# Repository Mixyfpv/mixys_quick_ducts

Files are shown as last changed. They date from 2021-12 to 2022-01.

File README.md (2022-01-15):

# Mixy's Quick Ducts
## What this is
Mixy's Quick Ducts are 5 inches ducts designed to fit most - if not all - 5 inch FPV drones in production today.

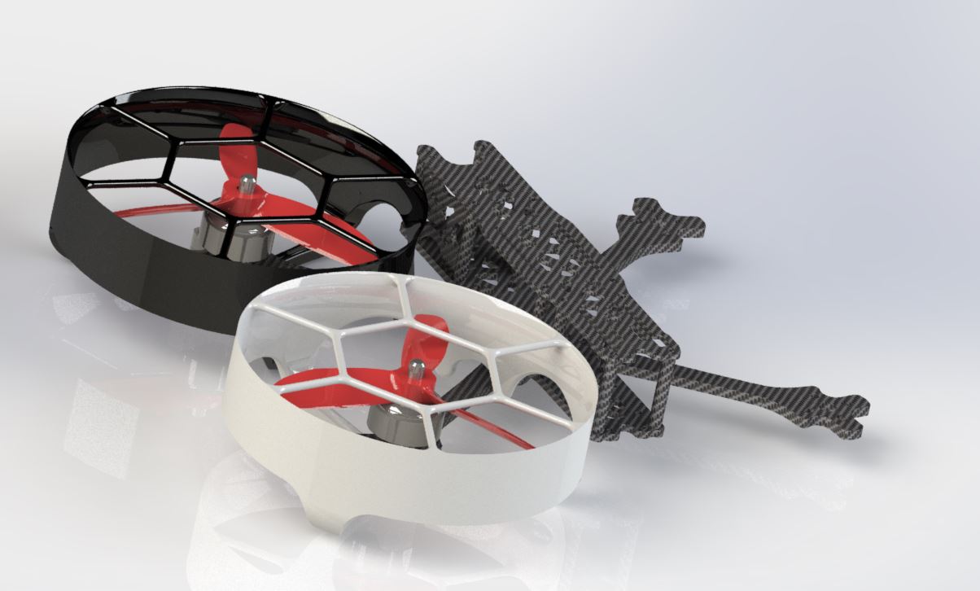
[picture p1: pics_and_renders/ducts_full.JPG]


These ducts were designed with one goal in mind, to be easy to use, and to be faster to put on and off your drone than currently available commercial solutions, as well as providing protection for bystanders when flying.

The ducts sit around the propeller disc. Their inside diameter is 5 inches.

It is expected that the duct will grind a bit of the props and its inside once you started the motors for the simple reason that the prop manufacturers tolerance to prop diameter varies. A lot. Around +- 1 mm. That is why you should not expect the prop to be perfectly flush against the inside of the duct.
3D printing imperfectiosn might also impact this.

The curve of the duct wall is an Eppler 423 airfoil which appear to be very suited for this use :
http://airfoiltools.com/airfoil/details?airfoil=e423-il

This ducts can be 3D printed. It has been tested with PLA+, regular PLA and PETG.
The arm mounts must be printed out of TPU.

## Some pics and renders

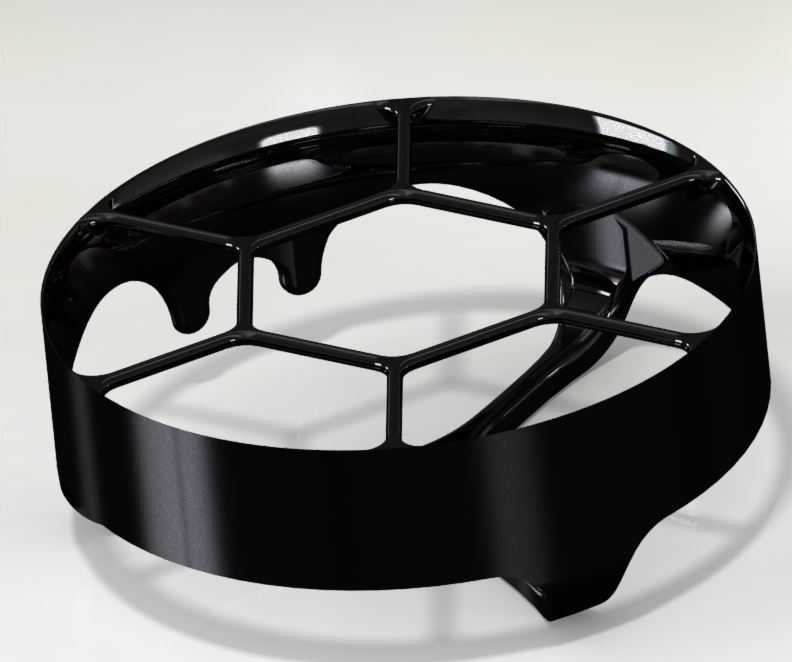
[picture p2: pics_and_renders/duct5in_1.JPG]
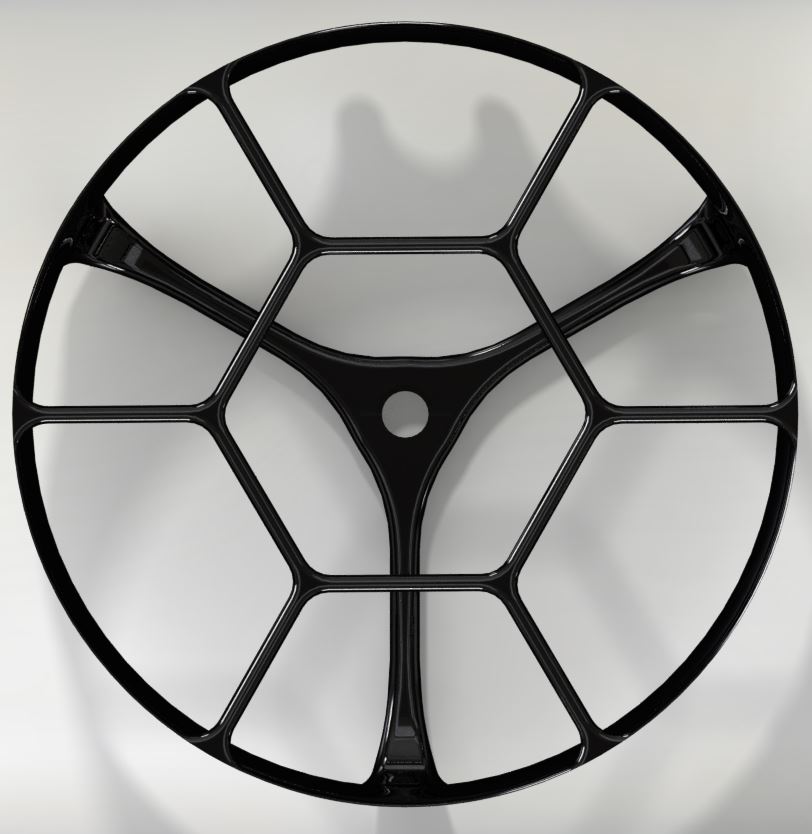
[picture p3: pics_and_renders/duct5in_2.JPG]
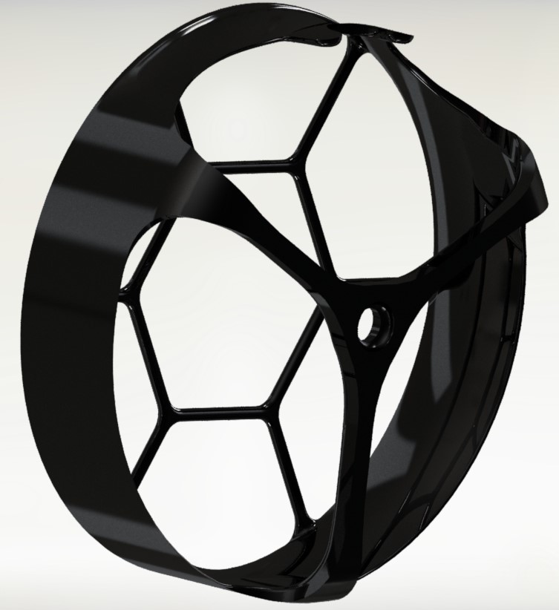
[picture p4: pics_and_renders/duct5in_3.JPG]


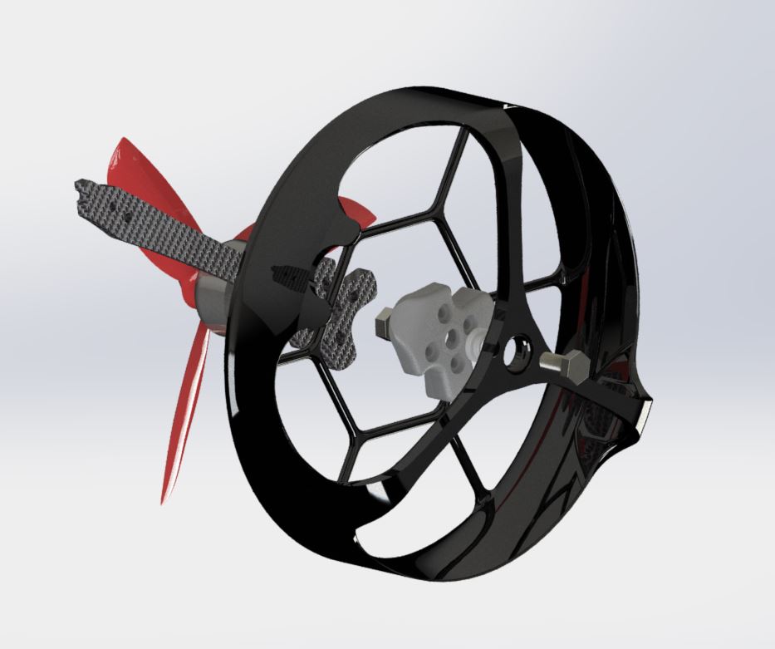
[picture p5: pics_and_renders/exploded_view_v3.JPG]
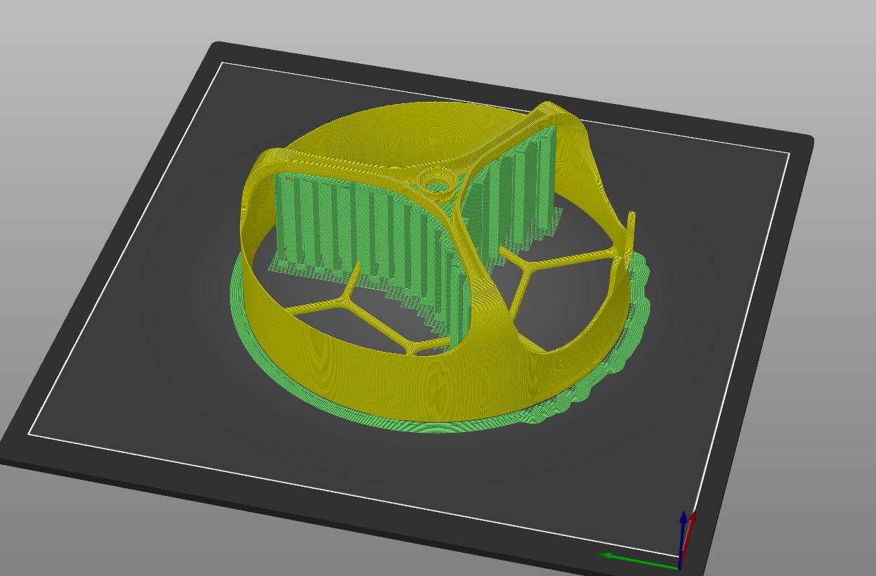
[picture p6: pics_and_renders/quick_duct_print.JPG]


## How to install
Here's a video describing the installation process : https://youtu.be/RlNhgd1YAD4

- Fix arm mounts on your frame of choice. Like any arm mounts use your M3 screws to go thought the TPU mount and secure it flush to the arm underneath the motor. REMEMBER TO PUT THE M5 NUT in its location before securing the arm mount or you will have to do it all over again. (See "How it works" section).
- (OPTIONNAL) Put the screw catcher in the hole on the inside face of the duct, and thread the bolt through it to hold it in place. Do not go to far or you won't fit the duct aroud the arm mount. (See "How it works" section).
- Push the duct around the prop through the gap between the duct arms and let one of the prop blades rest in the two "teeth". Make sure to angle these "teeth" toward the inde of the arm a it is where the arm will rest once fixed.

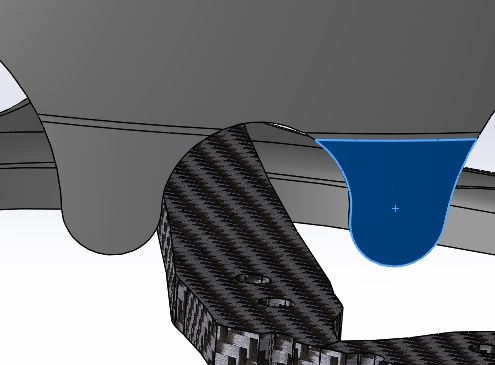
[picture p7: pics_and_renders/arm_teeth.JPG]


- Make sure the arms of the duct go around the front of the arm mount and the center top of the duct mount rest against the bottom of your arm mount.
- Center the M5 bolt to the center hole of the arm mount.
- Once the M5 bolt catches in the nut, make sure again that the teeth on the bottom side of the duct are going around the arm of the drone.
- Secure to your heart content. If properly secured you should be able to lift your drone by the duct with minimal vibrations.

## How it works
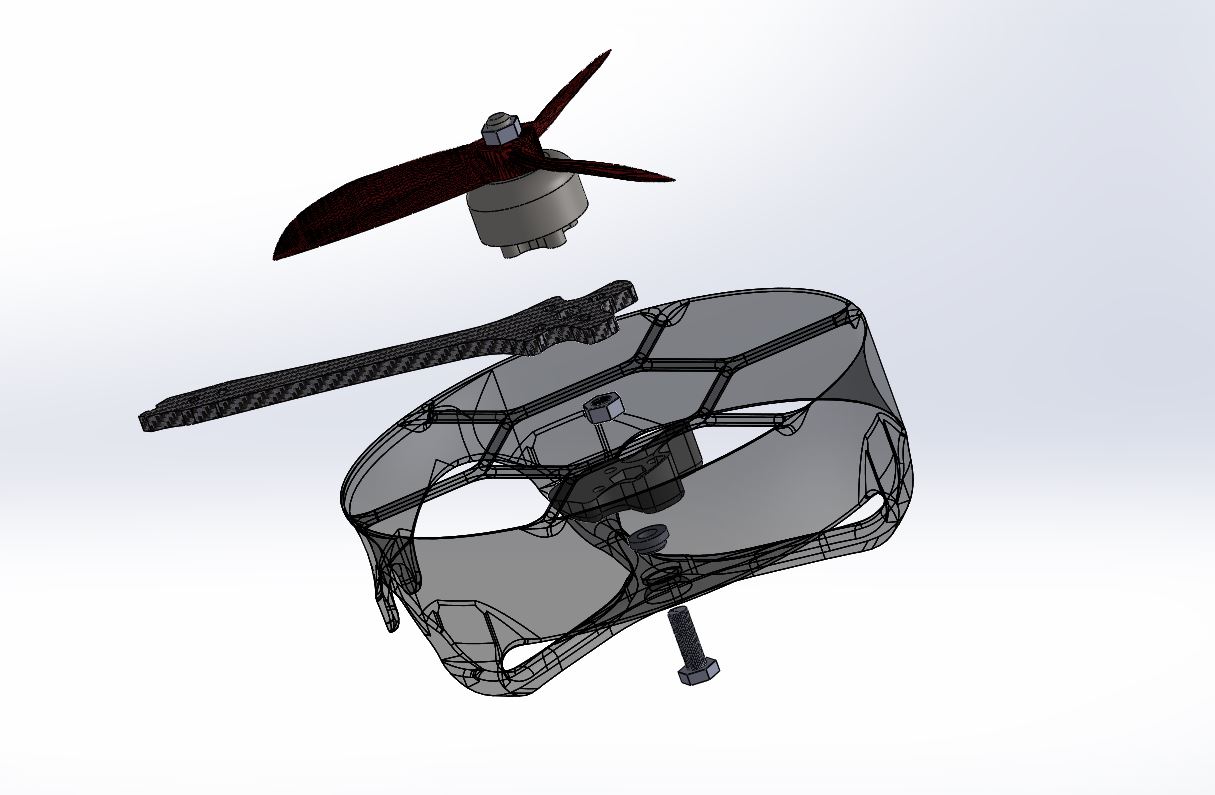
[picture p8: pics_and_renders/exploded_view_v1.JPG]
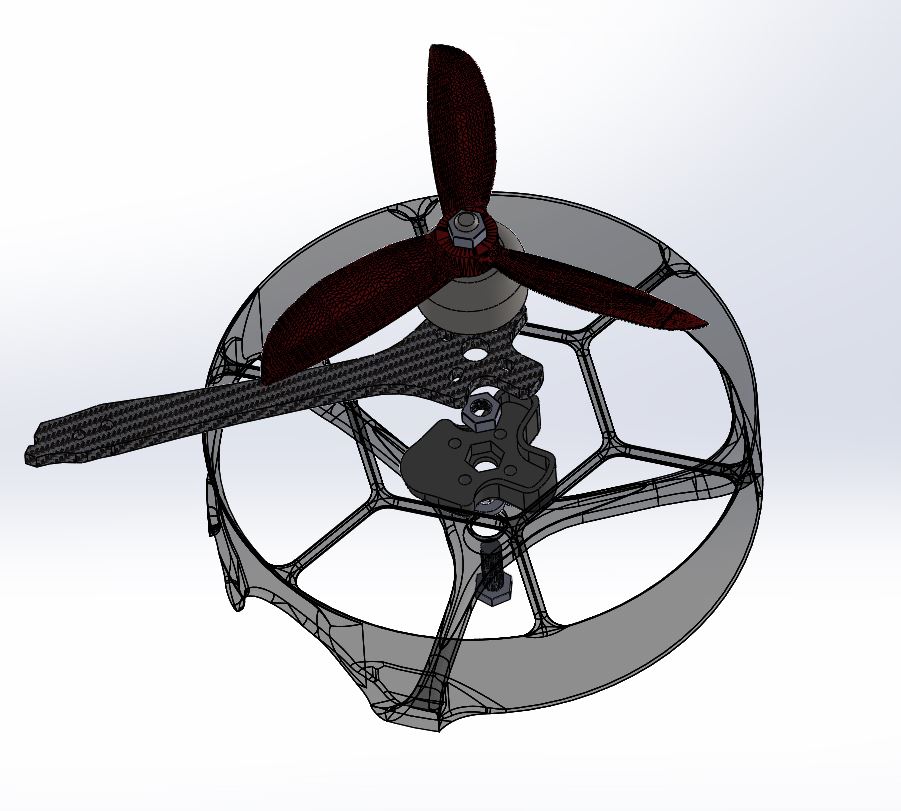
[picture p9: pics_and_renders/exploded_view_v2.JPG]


The best way to fix something like these ducts to your standard frame was to use the same nut and bolt size (M5) as 5 inches props we are used to.
Everyone is sure to have on hand the prop tool anywhere they fly, so this design fixation is centered aroud this idea.

Since the duct itself is frame agnostic, this means the duct holder (which is a dedicated arm pad) is the only dedicated part.
As you can see in the "arm_mount" directory, a few mounts are available.

All you need is an arm mount that will keep the nut centered on the prop axis and against the carbone frame.

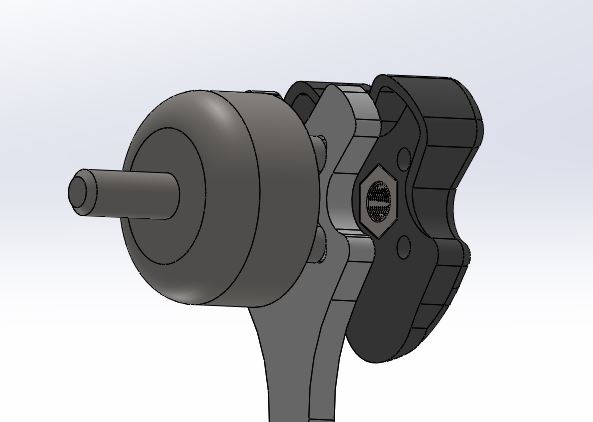
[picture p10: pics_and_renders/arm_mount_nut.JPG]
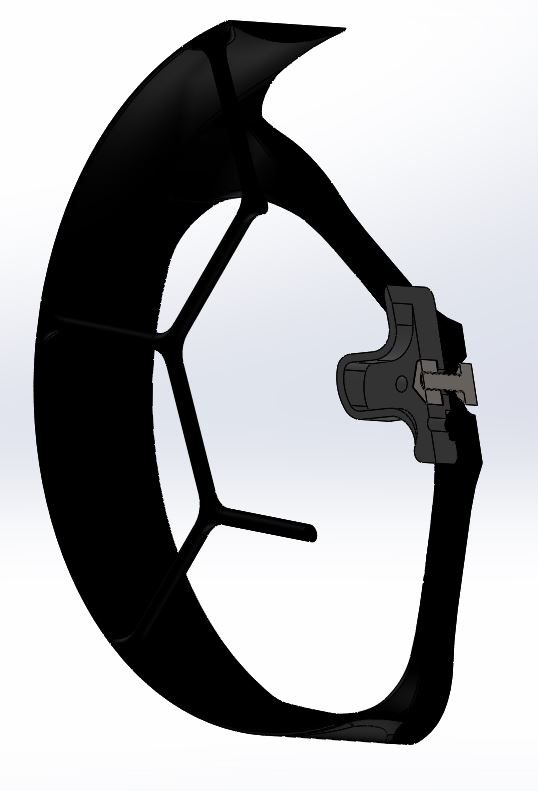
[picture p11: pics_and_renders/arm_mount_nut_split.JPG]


The M5 bolt length should be around 15mm. Too long and it will push agaisnt the carbone frame and won't properly secure the flat area of the duct. Too short and it won't catch in the nut and won't secure the duct to the frame.

Two "teeth" are used on the arm side of the duct to make sure the duct does not rotate around the bolt. Both the teeth are postionned around the arm of the drone and restrict the rotation.



On this same side, a divot as been made to the exterior of the duct to make it possible to rest agasint various frame top plates. For example, whilst the TBS Source One v4 provides enough space for it not to be needed, the Nazgul5 XL4 frame will need this space.

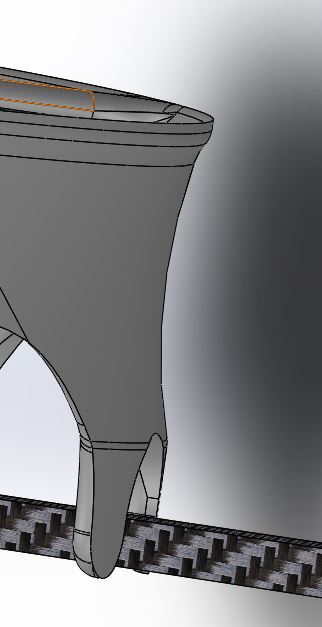
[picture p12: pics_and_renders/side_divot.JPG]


Lastly, for ease of use you can print a screw catcher (see "accessories") that will sit between the flat part of the duct and the underside of the arm mount. By driving the M5 bolt though this while it is in its definitive position, the bolt threads will catch and make the bolt secure to the duct, all the while it will be able to be released easily from the arm mount nut.

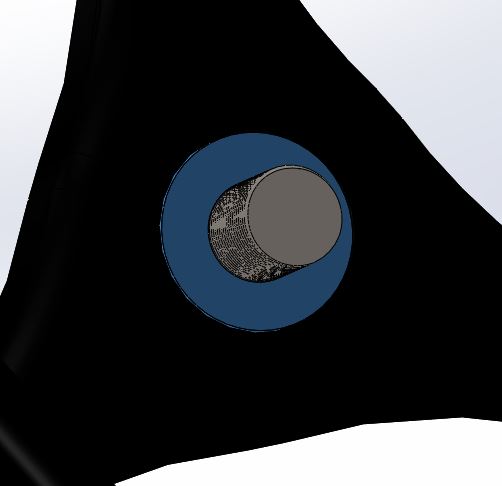
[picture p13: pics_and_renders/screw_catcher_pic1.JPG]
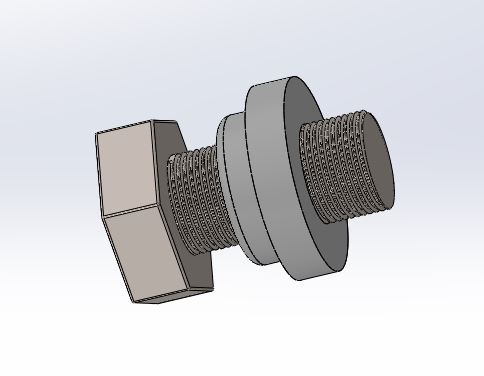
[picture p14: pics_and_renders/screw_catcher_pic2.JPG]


## What you need to use

|Type|Dimension|Quantity|
|----|----|----|
|Hexagonal nut|M5 (4mm thick)|1|
|Hexagonal bolt|M5x10mm|1|

- (OPTIONNAL) print the screw catcher and make sure it fits in the inside face of the duct mount.

And that's it.

## What it works with
Tested with these frames :
- Iflight Nazgul5 XL4
- Team Mistral AK47
- Team Mistral Dragunov
- TBS Source One V4/HD

## What this can become
This could become a great way for people that don't have the available resources to buy mutliple drones (like a dedicated cinewhoop) to be able to use their own drone and these 3D printable parts to fly around fragile things.

If you can't afford 350 bucks worth of drone to fly around people, use this and you'll be able to do it with whatever drone your currently flying.

Other dimensions will be added in the near future. And modify it however you want ! We want to see it grow.

Plus we should be able to add and swap parts on a drone in seconds instead of minutes. That is the final goal we want for this community.... The current record of putting the ducts on a drone is around 10 seconds per prop. Let's be even faster.

## Links
Thingiverse : https://www.thingiverse.com/thing:5200598

## License
 

This work is licensed under a Creative Commons Attribution 4.0 license, specifically CC BY 4.0.

https://creativecommons.org/licenses/by/4.0/

You can use, modify, share, even sell this, as long as credit is given.

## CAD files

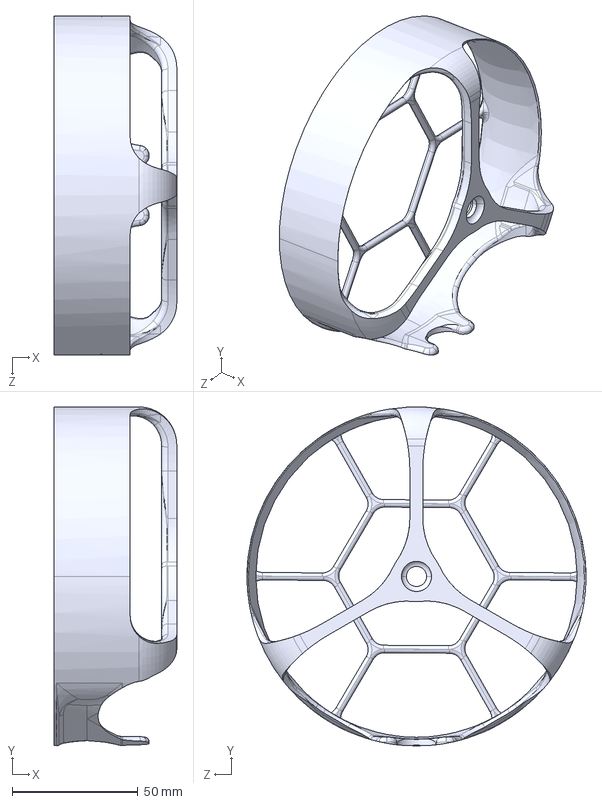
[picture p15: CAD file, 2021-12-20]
5in/mixys_quick_ducts_5in.STEP
48.8 x 134.9 x 135.0 mm

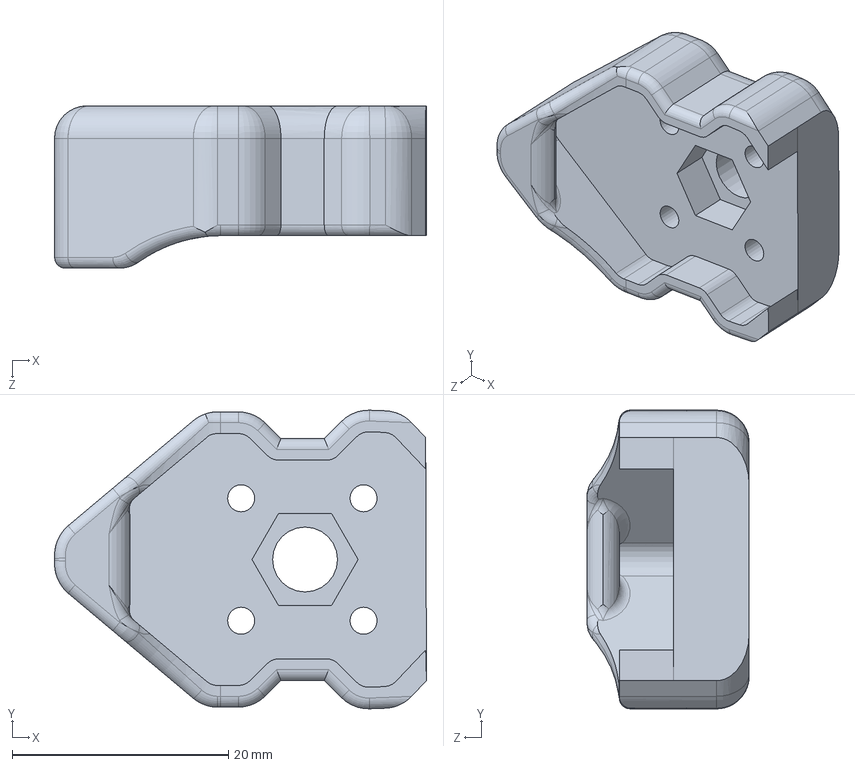
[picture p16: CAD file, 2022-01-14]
arm_mounts/ak47_quick_duct_mount.SLDPRT
34.4 x 27.6 x 15.0 mm

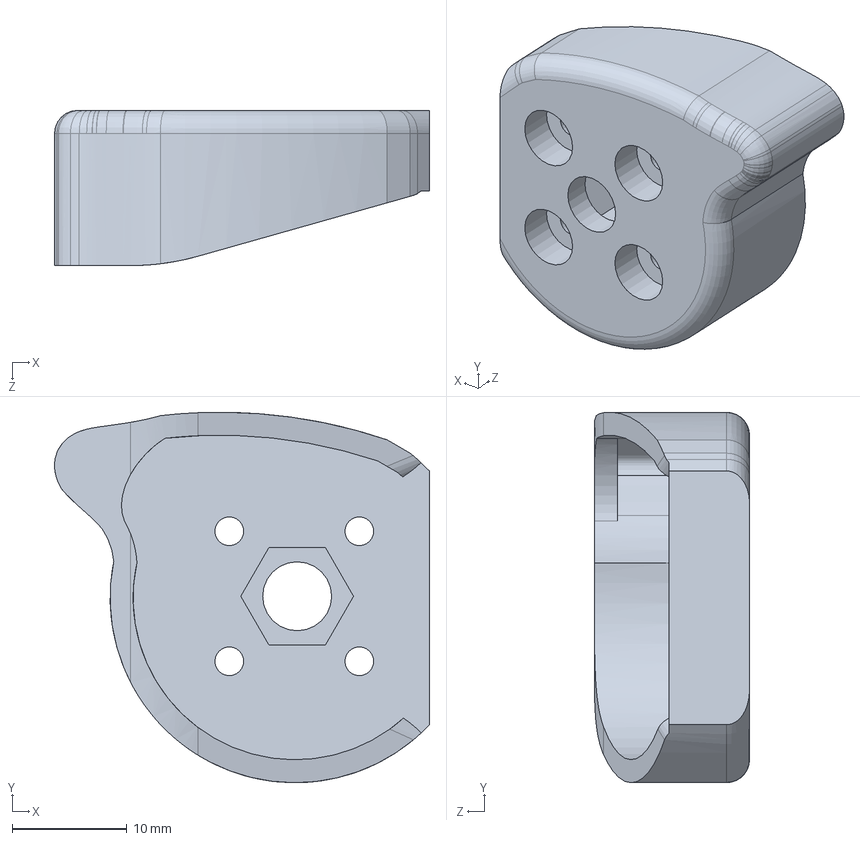
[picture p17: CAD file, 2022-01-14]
arm_mounts/nazgul5_xl4_quick_duct_mount.SLDPRT
32.6 x 32.2 x 13.5 mm

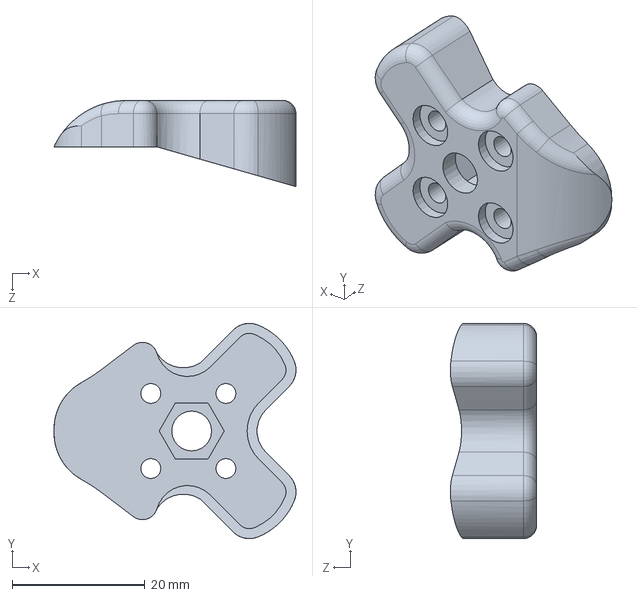
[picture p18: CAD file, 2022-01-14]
arm_mounts/tbssourceone_v4_quick_duct_mount.SLDPRT
36.5 x 32.5 x 13.0 mm

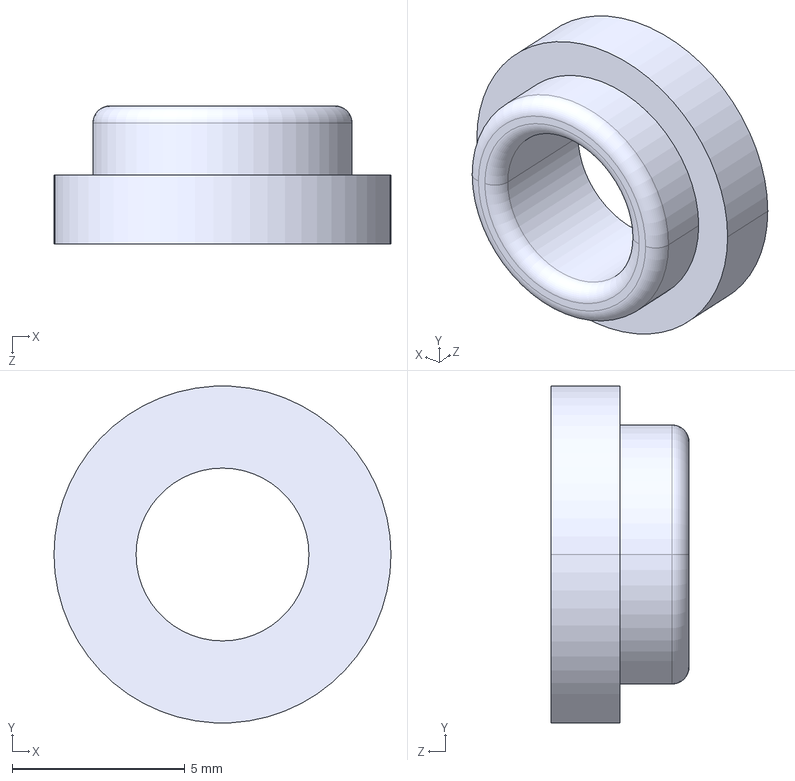
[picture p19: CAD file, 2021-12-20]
accessories/screw_lock.STEP
9.75 x 9.74 x 4.00 mm

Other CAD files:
5in/mixys_quick_ducts_5in.SLDPRT
5in/mixys_quick_ducts_5in.STL
accessories/screw_lock.SLDPRT

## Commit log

2021-12-20 Moving to 5 inch folder
    [mixys_quick_ducts_5in.SLDPRT, mixys_quick_ducts_5in.STEP, mixys_quick_ducts_5in.STL]
2021-12-20 Removing extra files
    [mixys_quick_ducts_5in.SLDPRT, mixys_quick_ducts_5in.STEP, mixys_quick_ducts_5in.STL]
2022-01-14 Add 1mm to mount bottom wall
    Add 1mm to bottom wall thickness to avoir ripping M5 nut in extreme crashes
    [ak47_quick_duct_mount.SLDPRT, nazgul5_xl4_quick_duct_mount.SLDPRT, tbssourceone_v4_quick_duct_mount.SLDPRT]
